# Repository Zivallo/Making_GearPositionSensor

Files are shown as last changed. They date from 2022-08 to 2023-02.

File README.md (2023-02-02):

# VJF125 기어포지션센서 개조
## 1. Topic
VJF125엔진의 변속기 부분을 사용한 DE-20(Team DOS, 2019.9-2021.2) 프로젝트에서 기어포지션센서를 개조하여 N(중립), 3단만 확인가능한 기존의 센서를 N(중립)단 포함 모든 단수를 확인 가능하도록 함

> DE-20 
## 2. Making
### 1) 작동방식

- VJF125 구조상 변속할 시 변속기의 기어를 움직여주는 Camshaft가 회전하게 되고 이 움직임에 따라 센서의 축이 회전


- 축이 회전하면서 센서 내부의 판 스프링이 함께 움직임
- 판 스프링의 중심부는 GND와 항상 접촉, 스프링 끝부분은 회전에 따라 납땜부(도체)와 접촉하게 됨
- 이 위치에 따라 기어 단수 판별
### 2) 제작
#### (1) 센서 중심부 절단 후 내용물 제거


> 중간에 서로 분리할 수 있게 생겼지만 당시 잘 되지 않아 그라인더로 절단하였습니다.

#### (2) GearPositionSenser.stl 파일을 이용해 3D 프린트 출력

#### (3) 츨력물 구멍에 전선을 넣고 끝부분에 남땜을 한 후 평평하도록 사포를 이용하여 간다.

> 재료를 PLA로 출력하다보니 납땜시 출력물이 녹는 경우가 있었습니다. 시간적 여유가 된다면 원통형 금속을 가공하거나 자석을 이용해 먼저 전선과 남땜을 한 후 3D 프린트 출력물과 조립하는 방법도 있을거 같습니다.
#### (4) 센서와 3D 프린트 출력물을 접착
> 실제로 큰 효과가 있는거 같진 않지만 중간 오일링을 넣을 수 있는 홈을 만들었습니다.
#### (5) Arduino Nano 와 연결

## 3. Result
### 1) Sensor

> 절단 후 남아 있는 센서의 길이가 짧아 오일링이 보이는데 추가로 에폭시를 이용해 마감하면 좋을거 같습니다.
### 2) 7-Segment Display(FND)
7-Segment Display 를 이용하여 드라이버에게 현재 단수 표시

> 당시 완성본에 대한 사진 및 영상이 남아있지 않아 제작 중 배선 접촉 불량으로 촬영한 사진으로 대체합니다.

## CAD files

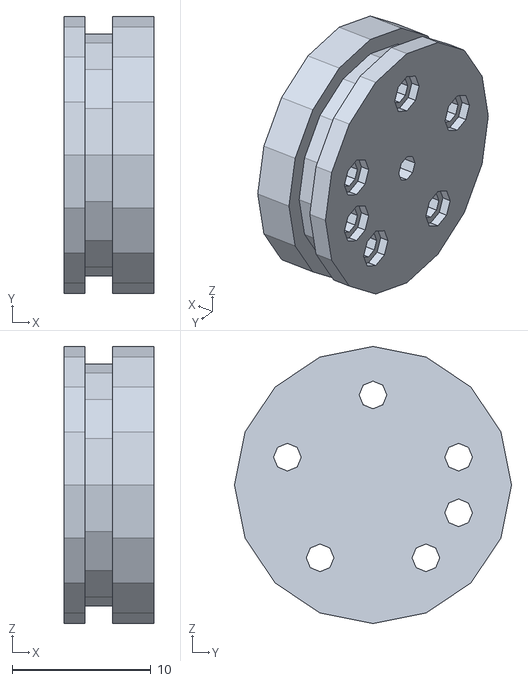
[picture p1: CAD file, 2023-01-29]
GearPositionSenser.stl
6.50 x 20.0 x 20.0

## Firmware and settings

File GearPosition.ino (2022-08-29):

byte digits[6][7]=
{
  {1,1,1,1,1,1,1},//0
  {0,1,1,0,0,0,0},//1
  {1,1,0,1,1,0,1},//2
  {1,1,1,1,0,0,1},//3
  {0,1,1,0,0,1,1},//4
  {1,0,1,1,0,1,1},//5
};
void setup() {
  Serial.begin(9600);
  pinMode(9,INPUT_PULLUP);
  pinMode(10,INPUT_PULLUP);
  pinMode(11,INPUT_PULLUP);
  pinMode(12,INPUT_PULLUP);
  pinMode(A1, INPUT_PULLUP);
}

void loop() {
  if(digitalRead(9) == LOW)
 {
  displayDigit(3);
  delay(500);
  Serial.print("3단\n");
 }
 else if(digitalRead(10) == LOW)
 {
  displayDigit(4);
  delay(500);
  Serial.print("4단\n");
 }
 else if(digitalRead(11) == LOW)
 {
  displayDigit(5);
  delay(500);
  Serial.print("5단\n");
 }
 else if(digitalRead(12) == LOW)
 {
  displayDigit(1);
  delay(500);
  Serial.print("1단\n");
 }
 else if( digitalRead(A1)== LOW)
 {
  displayDigit(0);
  delay(500);
  Serial.print("N\n");
 }
 else
 {
  displayDigit(2);
  delay(500);
  Serial.print("2단\n");
 }
}
void displayDigit(int num){
  int pin=2;
  for(int i=0; i<7; i++){
    digitalWrite(pin+i,digits[num][i]);
  }
}
